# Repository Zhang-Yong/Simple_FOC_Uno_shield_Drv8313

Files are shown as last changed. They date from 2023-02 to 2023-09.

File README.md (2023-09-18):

# Simple_FOC_Uno_shield_Drv8313
My Open Source Arduion Uno R3 BLDC FOC shield, use Drv8313 chip
KICAD5 Source file 
Optimze Layout, connect DGND with DRV8313 GND,adding I2C connector for AS5600
Tested work with simplefoc Arduino software
A Try Version for my standalone customerized FOC controller 




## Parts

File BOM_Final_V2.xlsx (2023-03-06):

Designator | Comment | 嘉立创元件编号 | FootPrint | Unit Price
C1 | 0.1u | C1591 | 0603 | 0.01
C2 | 0.1u | C1591 | 0603 | 0.01
C3 | 电解电容100u,50V | C165974 | 6.3x7.7mm | 2.35
C16 | 0.1u | C1591 | 0603 | 0.01
C17 | 0.1u | C1591 | 0603 | 0.01
C19 | 0.1uF | C1591 | 0603 | 0.01
C20 | 0.47_uF | C1623 | 0603 | 0.3
C21 | 10nF | C1589 | 0603 | 0.01
D7 | LED | C84270 | 1206 | 0.13
R1 | 4.7k | C23162 | 0603 | 0.005
R2 | 4.7k | C23162 | 0603 | 0.005
R6 | 3.3K | C22978 | 0603 | 0.005
R7 | 3.3K | C22978 | 0603 | 0.005
R8 | 3.3K | C22978 | 0603 | 0.005
R11 | 2K | C22975 | 0603 | 0.006
R12 | 0.01R, 电流采样电阻 | C104920 | 1206 | 1.6
R13 | 0.01R, 电流采样电阻 | C104920 | 1206 | 1.6
R16 | 10K | C25804 | 0603 | 0.005
U1 | L78M08,DPAK,ST | C158076 | DPAK,T0-252-2 | 1.5
U4 | INA240A2PW | C527535 | SOIC-8,4.4X3mm | 10
U5 | INA240A2PW | C527535 | SOIC-8,4.4X3mm | 10
U6 | TI 电机驱动芯片 | C92482 | HTSSOP-28-EP-4.5mm | 12

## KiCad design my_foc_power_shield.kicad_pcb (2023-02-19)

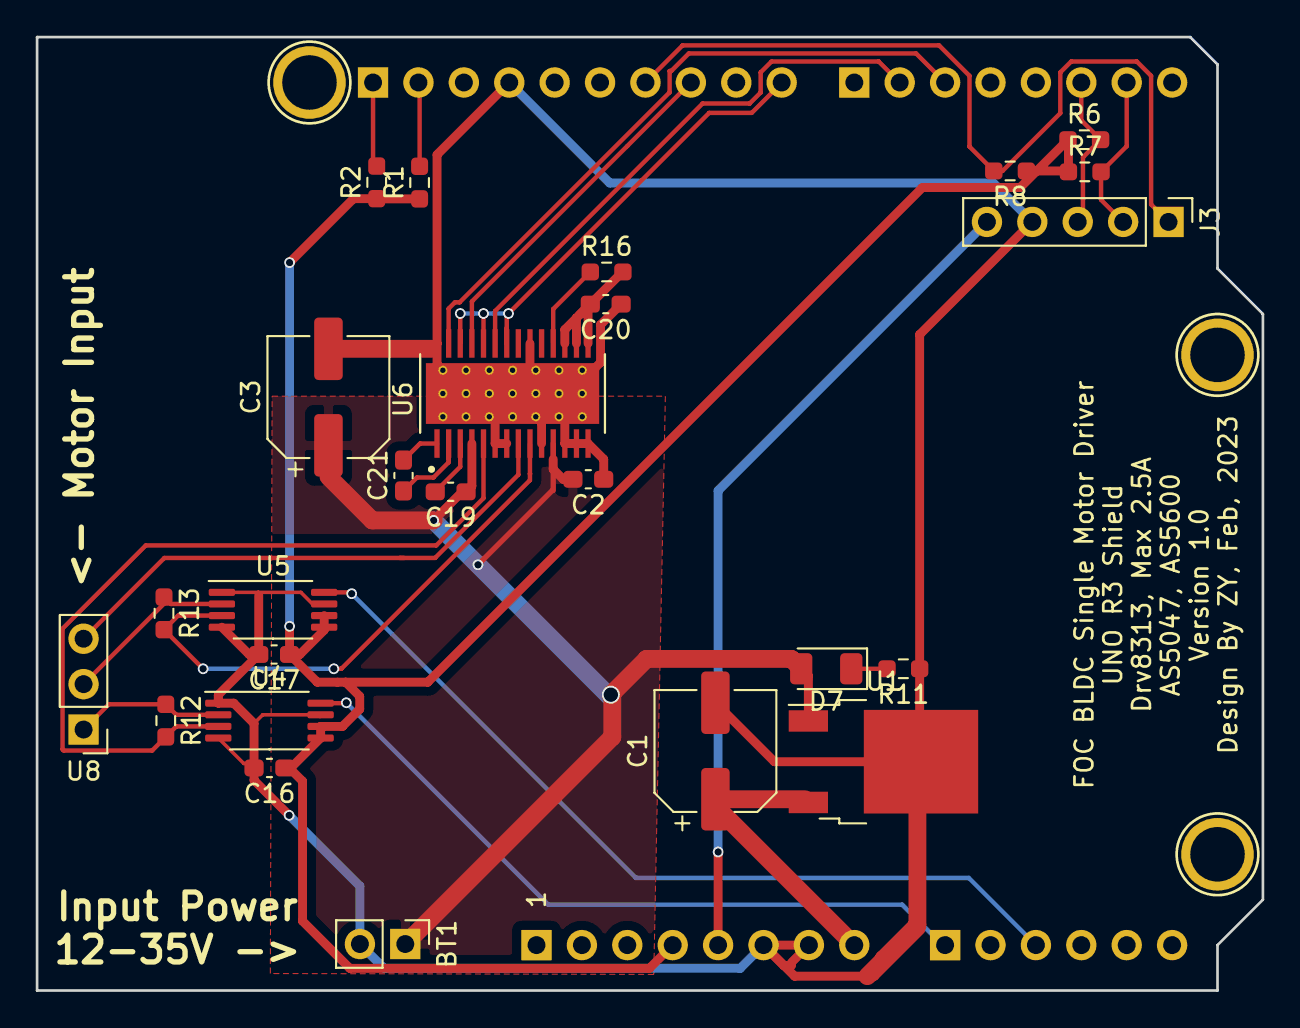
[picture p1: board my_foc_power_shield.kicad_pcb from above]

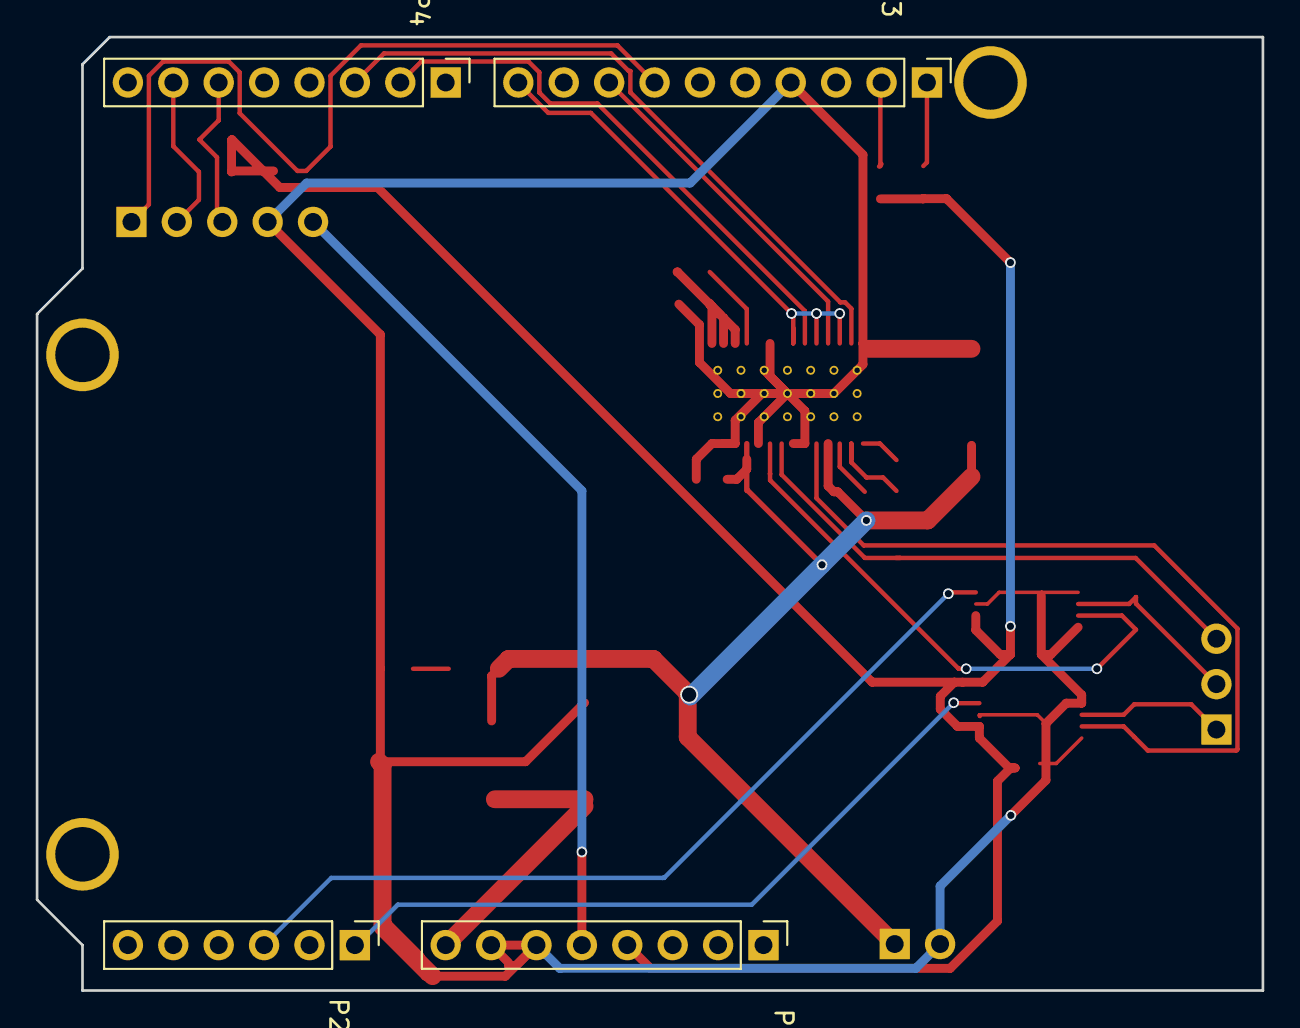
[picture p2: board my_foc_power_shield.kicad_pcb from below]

Board: 2 copper layers, 68.6 x 53.3 mm, 32 parts (4 on the bottom side), 27 nets.

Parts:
BT1: Battery; PinHeader_1x02_P2.54mm_Vertical
C1, C3: 100u,50V; CP_Elec_6.3x7.7
C2, C16, C17: 0.1u; C_0603_1608Metric_Pad1.08x0.95mm_HandSolder
C19: 0.1uF; C_0603_1608Metric_Pad1.08x0.95mm_HandSolder
C20: 0.47 uF; C_0603_1608Metric_Pad1.08x0.95mm_HandSolder
C21: 10nF; C_0603_1608Metric_Pad1.08x0.95mm_HandSolder
D7: LED; LED_1206_3216Metric
J3: AS5047; PinHeader_1x05_P2.54mm_Vertical
P1: Power; PinHeader_1x08_P2.54mm_Vertical
P2: Analog; PinHeader_1x06_P2.54mm_Vertical
P3: Digital; PinHeader_1x10_P2.54mm_Vertical
P4: Digital; PinHeader_1x08_P2.54mm_Vertical
P6, P7, P8: CONN_01X01; Arduino_1pin
R1, R2, R6, R7, R8: 3.3K; R_0603_1608Metric_Pad0.98x0.95mm_HandSolder
R11: 2K; R_0603_1608Metric_Pad0.98x0.95mm_HandSolder
R12, R13: 0.01R; R_0603_1608Metric_Pad0.98x0.95mm_HandSolder
R16: 10K; R_0603_1608Metric_Pad0.98x0.95mm_HandSolder
U1: L7808; TO-252-2
U4, U5: INA240A2PW; TSSOP-8_4.4x3mm_P0.65mm
U6: DRV8313PWP; drv8313pwp
U8: Motor Inputs; PinHeader_1x03_P2.54mm_Vertical

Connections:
+3V3: C16.1, C17.1, P1.4, R1.1, R2.1, R6.1, R7.1, R8.1, U4.5, U4.6, U5.5, U5.6
+5V: J3.5, P1.5
/DRV_EN_8: P3.10, U6.22, U6.24, U6.26
/DRV_FAULT: R16.1, U6.18
/Encoder_A_D2: J3.3, P4.6, R6.2
/Encoder_B_D1: J3.2, P4.7, R7.2
/Encoder_Z_D11: J3.1, P3.7, R8.2
/MOTOR_A: R12.1, U4.2, U8.1
/MOTOR_A_CS: R12.2, U4.3, U6.5
/MOTOR_B: R13.1, U5.2, U8.2
/MOTOR_B_CS: R13.2, U5.3, U6.9
/MOTOR_C: U6.8, U8.3
/PWM_A_5: P4.3, U6.27
/PWM_B_10: P3.8, U6.25
/PWM_C_6: P4.2, U6.23
/SCL: P3.1, R2.2
/SDA: P3.2, R1.2
/SENSE_A_A0: P2.1, U4.8
/SENSE_B_A2: P2.3, U5.8
/V3P3: C20.2, R16.2, U6.15, U6.16, U6.17
/Vin: C1.1, P1.8, U1.3
GNDA: BT1.2, C1.2, C2.1, C3.2, C16.2, C17.2, C20.1, J3.4, P1.6, P1.7, P3.4, R11.1, U1.2, U4.1, U4.4, U4.7, U5.1, U5.4, U5.7, U6.6, U6.7, U6.10, U6.12, U6.13, U6.14, U6.20, U6.28, U6.29
unnamed: C19.2, U6.3
unnamed: C21.1, U6.2
unnamed: C21.2, U6.1
unnamed: D7.1, R11.2
VCC_IN: BT1.1, C2.2, C3.1, C19.1, D7.2, U1.1, U6.4, U6.11

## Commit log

2023-02-19 Add files via upload
    Kicad design file, includes schematic and pcb
    [my_foc_power_shield.kicad_pcb, my_foc_power_shield.sch]
2023-02-19 Add files via upload
    Gerbe file
    [BOM_Final.xlsx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]
2023-03-06 Update README.md
    Optimize layout, adding AS5600 connector
    Test work with simplefoc Arduino Software
2023-03-06 Add files via upload
    Update V2 Version of KICAD schematic and layout file
2023-03-06 Add files via upload
    V2 BOM File
    [BOM_Final_V2.xlsx]
